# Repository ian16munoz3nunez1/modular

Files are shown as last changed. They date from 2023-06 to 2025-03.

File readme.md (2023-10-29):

# Proyecto Modular (Equipo Amistad) 😉

## Archivos binarios

- [MicroPython](https://micropython.org/download/esp32)
- [esp32cam](https://github.com/lemariva/micropython-camera-driver)

## Librerias Python

- ***sockets*** `pip install sockets`
- ***opencv*** `pip install opencv-contrib-python`
- ***numpy*** `pip install numpy` 
- ***matplotlib*** `pip install matplotlib`
- ***thonny*** `pip install thonny-esp`
- ***pyserial*** `pip install pyserial`
- ***esptool*** `pip install esptool`
- ***ampy*** `pip install adafruit-ampy`

## Comandos y programas

### Windows

Listar los dispositivos conectados a los puertos:
`py -m serial.tools.list_ports`

Borrar la memoria del esp32:
`esptool --chip esp32 --port COM* erase_flash`

Cargar el archivo binario a la placa esp32:
`esptool --chip esp32 --port COM* --baud 460800 write_flash -z 0x1000 <esp32version>.bin`

Cargar un archivo *Python* a la esp32:
`ampy --port COM* put main.py`

Obtener el contenido de un archivo:
`ampy --port COM* get main.py`

Listar los archivos dentro de la placa:
`ampy --port COM* ls`

Crear conexión serial con la esp32 en PuTTY:

- Puerto: ***COM\****
- Velocidad: ***115200 bauds***

#### Configurar Thonny para esp32cam

Ir a ***Thonny***:

`Tools > Open Thonny data folder...`

Agregar al archivo ***configuration.ini*** en la sección ***ESP32***

```
[ESP32]
rts = False
dtr = False
```

### Linux

Listar los dispositivos conectados a los puertos:
`python3 -m serial.tools.list_ports`

Borrar la memoria del esp32:
`esptool.py --chip esp32 --port /dev/ttyUSB* erase_flash`

Cargar el archivo binario a la placa esp32:
`esptool.py --chip esp32 --port /dev/ttyUSB* --baud 460800 write_flash -z 0x1000 <esp32version>.bin`

Cargar un archivo *Python* a la esp32:
`ampy --port /dev/ttyUSB* put main.py`

Obtener el contenido de un archivo:
`ampy --port /dev/ttyUSB* get main.py`

Listar los archivos dentro de la placa:
`ampy --port /dev/ttyUSB* ls`

Crear conexión serial con la esp32:
`picocom /dev/ttyUSB* -b 115200`

Crear conexión serial con la esp32cam:
`picocom /dev/ttyUSB* -b 115200 --lower-dtr --lower-rts`

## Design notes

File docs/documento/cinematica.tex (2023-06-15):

\sffamily\large\justify

\pagenumbering{arabic}

\section{Cinemática directa}

\subsection{Modelado del \emph{youBot Arm}}

\begin{figure}[h!]
    \centering
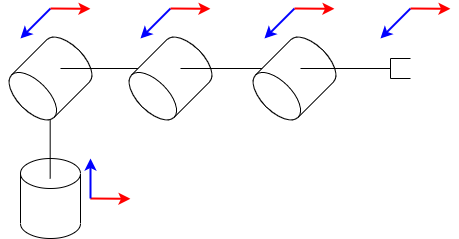
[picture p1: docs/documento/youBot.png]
    
    \caption{\sffamily youBot Arm}
    \label{fig:youBotArmModel}
\end{figure}

\subsection{Fórmulas y propiedades}

\begin{equation*}
    ^{n-1}T_n =
    \begin{bmatrix}
        C_{\theta_n} & -S_{\theta_n}C_{\alpha_n} & S_{\theta_n}S_{\alpha_n} & a_nC_{\theta_n} \\
        S_{\theta_n} & C_{\theta_n}C_{\alpha_n} & -C_{\theta_n}S_{\alpha_n} & a_nS_{\theta_n} \\
        0 & S_{\alpha_n} & C_{\alpha_n} & d_n \\
        0 & 0 & 0 & 1
    \end{bmatrix}
\end{equation*}

\begin{equation*}
    \begin{split}
        \sin(\alpha \pm \beta) & = \sin(\alpha)\cos(\beta) \pm \cos(\alpha)\sin(\beta) \\
        \cos(\alpha \pm \beta) & = \cos(\alpha)\cos(\beta) \mp \sin(\alpha)\sin(\beta)
    \end{split}
\end{equation*}

\newpage
\subsection{Tabla de parámetros \emph{Denavit-Hartenberg}}

\begin{table}[h!]
    \centering\sffamily\large

    \begin{tabular}{|c|c|c|c|c|}
        \hline
        & $\alpha$ & $a$ & $d$ & $\theta$ \\
        \hline
        1 & $\frac{\pi}{2}$ & $0$ & $d_1$ & $0$ \\
        \hline
        2 & $0$ & $a_2$ & $0$ & $0$ \\
        \hline
        3 & $0$ & $a_3$ & $0$ & $0$ \\
        \hline
        4 & $0$ & $a_4$ & $0$ & $0$ \\
        \hline
    \end{tabular}

    \caption{\sffamily Tabla de parámetros \emph{Denavit-Hartenberg}}
    \label{tab:tablaDH}
\end{table}

\subsection{Matrices de transformación}

\begin{equation*}
    \tcboxmath[colback=white, colframe=black]{
    ^0T_1 =
    \begin{bmatrix}
        C_1 & 0 & S_1 & 0 \\
        S_1 & 0 & -C_1 & 0 \\
        0 & 0 & 1 & 0 \\
        0 & 0 & 0 & 1
    \end{bmatrix}
    }
    \quad\quad
    ^1T_2 =
    \begin{bmatrix}
        C_2 & -S_2 & 0 & a_2C_2 \\
        S_2 & C_2 & 0 & a_2S_2 \\
        0 & 0 & 1 & 0 \\
        0 & 0 & 0 & 1
    \end{bmatrix}
\end{equation*}

\begin{equation*}
    ^2T_3 =
    \begin{bmatrix}
        C_3 & -S_3 & 0 & a_3C_3 \\
        S_3 & C_3 & 0 & a_3S_3 \\
        0 & 0 & 1 & 0 \\
        0 & 0 & 0 & 1
    \end{bmatrix}
    \quad\quad
    ^3T_4 =
    \begin{bmatrix}
        C_4 & -S_4 & 0 & a_4C_4 \\
        S_4 & C_4 & 0 & a_4S_4 \\
        0 & 0 & 1 & 0 \\
        0 & 0 & 0 & 1
    \end{bmatrix}
\end{equation*}

\begin{equation*}
    ^0T_4 = {^0T_1} \, {^1T_2} \, {^2T_3} \, {^3T_4}
\end{equation*}

\newpage
\subsection{Cinemática directa del \emph{youBot Arm}}

\begin{equation*}
    \tcboxmath[colback=white, colframe=black]{
    ^0T_2 =
    \begin{bmatrix}
        C_1C_2 & -C_1S_2 & S_1 & a_2C_1C_2 \\
        S_1C_2 & -S_1S_2 & -C_1 & a_2S_1C_2 \\
        S_2 & C_2 & 0 & a_2S_2 + d_1 \\
        0 & 0 & 0 & 1
    \end{bmatrix}
    }
\end{equation*}

{\small
\begin{equation*}
    ^0T_3 =
    \begin{bmatrix}
        C_1C_2C_3 - C_1S_2S_3 & -C_1C_2S_3 - C_1S_2C_3 & S_1 & a_3C_1C_2C_3 - a_3C_1S_2S_3 + a_2C_1C_2 \\
        S_1C_2C_3 - S_1S_2S_3 & -S_1C_2S_3 - S_1S_2C_3 & -C_1 & a_3S_1C_2C_3 - a_3S_1S_2S_3 + a_2S_1C_2 \\
        S_2C_3 + C_2S_3 & -S_2S_3 + C_2C_3 & 0 & a_3S_2C_3 + a_3C_2S_3 + a_2S_2 + d_1 \\
        0 & 0 & 0 & 1
    \end{bmatrix}
\end{equation*}
}

\begin{equation*}
    \tcboxmath[colback=white, colframe=black]{
    ^0T_3 =
    \begin{bmatrix}
        C_1C_{23} & -C_1S_{23} & S_1 & a_3C_1C_{23} + a_2C_1C_2 \\
        S_1C_{23} & -S_1S_{23} & -C_1 & a_3S_1C_{23} + a_2S_1C_2 \\
        S_{23} & C_{23} & 0 & a_3S_{23} + a_2S_2 + d_1 \\
        0 & 0 & 0 & 1
    \end{bmatrix}
    }
\end{equation*}

{\scriptsize
\begin{equation*}
    ^0T_4 =
    \begin{bmatrix}
        C_1C_{23}C_4 - C_1S_{23}S_4 & -C_1C_{23}S_4 - C_1S_{23}C_4 & S_1 & a_4C_1C_{23}C_4 - a_4C_1S_{23}S_4 + a_3C_1C_{23} + a_2C_1C_2 \\
        S_1C_{23}C_4 - S_1S_{23}S_4 & -S_1C_{23}S_4 - S_1S_{23}C_4 & -C_1 & a_4S_1C_{23}C_4 - a_4S_1S_{23}S_4 + a_3S_1C_{23} + a_2S_1C_2 \\
        S_{23}C_4 + C_{23}S_4 & -S_{23}S_4 + C_{23}C_4 & 0 & a_4S_{23}C_4 + a_4C_{23}S_4 + a_3S_{23} + a_2S_2 + d_1 \\
        0 & 0 & 0 & 1
    \end{bmatrix}
\end{equation*}
}

\begin{equation*}
    ^0T_4 =
    \begin{bmatrix}
        C_1C_{234} & -C_1S_{234} & S_1 & a_4C_1C_{234} + a_3C_1C_{23} + a_2C_1C_2 \\
        S_1C_{234} & -S_1S_{234} & -C_1 & a_4S_1C_{234} + a_3S_1C_{23} + a_2C_1C_2 \\
        S_{234} & C_{234} & 0 & a_4S_{234} + a_3S_{23} + a_2S_2 + d_1 \\
        0 & 0 & 0 & 1
    \end{bmatrix}
\end{equation*}

\begin{equation*}
    \tcboxmath[colback=white, colframe=black]{
    ^0T_4 =
    \begin{bmatrix}
        C_1C_{234} & -C_1S_{234} & S_1 & C_1 ( a_4C_{234} + a_3C_{23} + a_2C_2 ) \\
        S_1C_{234} & -S_1S_{234} & -C_1 & S_1 ( a_4C_{234} + a_3C_{23} + a_2C_2 ) \\
        S_{234} & C_{234} & 0 & a_4S_{234} + a_3S_{23} + a_2S_2 + d_1 \\
        0 & 0 & 0 & 1
    \end{bmatrix}
    }
\end{equation*}

\newpage
\subsection{Cinemática directa de la plataforma omnidireccional}

\begin{equation*}
    \begin{bmatrix}
        \dot{x} \\
        \dot{y} \\
        \dot{\theta}
    \end{bmatrix} =
    \begin{bmatrix}
        \cos(\theta) & -\sin(\theta) & 0 \\
        \sin(\theta) & \cos(\theta) & 0 \\
        0 & 0 & 1
    \end{bmatrix}
    \begin{bmatrix}
        1 & -1 & -(L+l) \\
        1 & 1 & (L+l) \\
        1 & 1 & -(L+l) \\
        1 & -1 & (L+l)
    \end{bmatrix}^\dagger
    \begin{bmatrix}
        v_1 \\
        v_2 \\
        v_3 \\
        v_4
    \end{bmatrix}
\end{equation*}

\subsection{Cinemática inversa de la plataforma omnidireccional}

\begin{equation*}
    \begin{bmatrix}
        v_1 \\
        v_2 \\
        v_3 \\
        v_4
    \end{bmatrix} =
    \begin{bmatrix}
        1 & -1 & -(L+l) \\
        1 & 1 & (L+l) \\
        1 & 1 & -(L+l) \\
        1 & -1 & (L+l)
    \end{bmatrix}
    \begin{bmatrix}
        \cos(\theta) & -\sin(\theta) & 0 \\
        \sin(\theta) & \cos(\theta) & 0 \\
        0 & 0 & 1
    \end{bmatrix}^\top
    \begin{bmatrix}
        \dot{x} \\
        \dot{y} \\
        \dot{\theta}
    \end{bmatrix}
\end{equation*}

\begin{equation*}
    \begin{bmatrix}
        v_1 \\
        v_2 \\
        v_3 \\
        v_4
    \end{bmatrix} =
    \begin{bmatrix}
        \sqrt{2}\sin(\alpha) & -\sqrt{2}\cos(\alpha) & -(L+l) \\
        \sqrt{2}\cos(\alpha) & \sqrt{2}\sin(\alpha) & (L+l) \\
        \sqrt{2}\cos(\alpha) & \sqrt{2}\sin(\alpha) & -(L+l) \\
        \sqrt{2}\sin(\alpha) & -\sqrt{2}\cos(\alpha) & (L+l)
    \end{bmatrix}
    \begin{bmatrix}
        \dot{x} \\
        \dot{y} \\
        \dot{\theta}
    \end{bmatrix}
\end{equation*}

\begin{equation*}
    \alpha = \theta + \frac{\pi}{4}
\end{equation*}

\newpage
\subsection{Cinemática directa desde el origen hasta el efector final}

\renewcommand{\labelitemi}{$\bullet$}
\begin{itemize}
    \item \textbf{w:} Eje coordenado del origen.
    \item \textbf{p:} Eje coordenado adherido a la plataforma.
    \item \textbf{b:} Eje coordenado de la base del manipulador.
    \item \textbf{e:} Eje coordenado del actuador final.
\end{itemize}

\begin{equation*}
    ^wT_e = {^wT_p} \, {^pT_b} \, {^bT_e}
\end{equation*}

\begin{equation*}
    \tcboxmath[colback=white, colframe=black]{
    ^wT_p =
    \begin{bmatrix}
        \cos(\theta_p) & -\sin(\theta_p) & 0 & x_p \\
        \sin(\theta_p) & \cos(\theta_p) & 0 & y_p \\
        0 & 0 & 1 & 0 \\
        0 & 0 & 0 & 1
    \end{bmatrix}
    }
\end{equation*}

\hspace{0.5cm} Con $x_p$ y $y_p$ como la posición del robot y $\theta_p$ como la
orientación.

\begin{equation*}
    \tcboxmath[colback=white, colframe=black]{
    ^pT_b =
    \begin{bmatrix}
        1 & 0 & 0 & 0.170 \\
        0 & 1 & 0 & 0 \\
        0 & 0 & 1 & 0.060 \\
        0 & 0 & 0 & 1
    \end{bmatrix}
    }
\end{equation*}

\begin{equation*}
    \tcboxmath[colback=white, colframe=black]{
    ^bT_e = {^0T_4}
    }
\end{equation*}

\begin{equation*}
    \tcboxmath[colback=white, colframe=black]{
    ^wT_b =
    \begin{bmatrix}
        \cos(\theta_p) & -\sin(\theta_p) & 0 & 0.170\cos(\theta_p) + x_p \\
        \sin(\theta_p) & \cos(\theta_p) & 0 & 0.170\sin(\theta_p) + y_p \\
        0 & 0 & 1 & 0.060 \\
        0 & 0 & 0 & 1
    \end{bmatrix}
    }
\end{equation*}

\newpage
{\normalsize
\begin{equation*}
    \tcboxmath[colback=white, colframe=black]{
    \begin{split}
        x & = C_\theta C_1( a_4C_{234}+a_3C_{23}+a_2C_2 ) - S_\theta S_1( a_4C_{234}+a_3C_{23}+a_2C_2 ) + 0.170C_\theta + x_p \\
        y & = S_\theta C_1( a_4C_{234}+a_3C_{23}+a_2C_2 ) + C_\theta S_1( a_4C_{234}+a_3C_{23}+a_2C_2 ) + 0.170S_\theta + y_p \\
        z & = a_4S_{234} + a_3S_{23} + a_2S_2 + d_1 + 0.060 \\
    \end{split}
    }
\end{equation*}
}

{\normalsize
\begin{equation*}
    \tcboxmath[colback=white, colframe=black]{
    ^wT_e =
    \begin{bmatrix}
        C_\theta C_1C_{234} - S_\theta S_1C_{234} & -C_\theta C_1S_{234} + S_\theta S_1S_{234} & C_\theta S_1 + S_\theta C_1 & x \\
        S_\theta C_1 C_{234} + C_\theta S_1C_{234} & -S_\theta C_1S_{234} - C_\theta S_1S_{234} & S_\theta S_1 - C_\theta C_1 & y \\
        S_{234} & C_{234} & 0 & z \\
        0 & 0 & 0 & 1
    \end{bmatrix}
    }
\end{equation*}
}

{\normalsize
\begin{equation*}
    \tcboxmath[colback=white, colframe=black]{
    ^wT_e =
    \begin{bmatrix}
        C_{\theta 1}C_{234} & -C_{\theta 1}S_{234} & S_{\theta 1} & C_{\theta 1} ( a_4C_{234} + a_3C_{23} + a_2C_2 ) + 0.170C_\theta + x_p \\
        S_{\theta 1}C_{234} & -S_{\theta 1}S_{234} & -C_{\theta 1} & S_{\theta 1} ( a_4C_{234} + a_3C_{23} + a_2C_2 ) + 0.170S_\theta + y_p \\
        S_{234} & C_{234} & 0 & a_4S_{234} + a_3S_{23} + a_2S_2 + d_1 + 0.060 \\
        0 & 0 & 0 & 1
    \end{bmatrix}
    }
\end{equation*}
}

\subsection{Cinemática diferencial}

\begin{equation*}
    J_v(q) =
    \begin{bmatrix}
        \dfrac{\partial p_1(q)}{\partial q_1} & \dfrac{\partial p_1(q)}{\partial q_2} & \dotsc & \dfrac{\partial p_1(q)}{\partial q_n} \\
        \dfrac{\partial p_2(q)}{\partial q_1} & \dfrac{\partial p_2(q)}{\partial q_2} & \dotsc & \dfrac{\partial p_2(q)}{\partial q_n} \\
        \vdots & \vdots & \ddots & \vdots \\
        \dfrac{\partial p_m(1)}{\partial q_1} & \dfrac{\partial p_m(q)}{\partial q_2} & \dotsc & \dfrac{\partial p_m(q)}{\partial q_n}
    \end{bmatrix}
\end{equation*}

\begin{equation*}
    \begin{split}
        t_x & = C_{\theta 1} ( a_4C_{234} + a_3C_{23} + a_2C_2 ) + 0.170C_\theta + x_p \\
        t_y & = S_{\theta 1} ( a_4C_{234} + a_3C_{23} + a_2C_2 ) + 0.170S_\theta + y_p \\
        t_z & = a_4S_{234} + a_3S_{23} + a_2S_2 + d_1 + 0.060
    \end{split}
\end{equation*}

\newpage
\begin{equation*}
    \begin{split}
        \frac{\partial t_x}{\partial x_p} & = 1 \\
        \frac{\partial t_x}{\partial y_p} & = 0 \\
        \frac{\partial t_x}{\partial \theta_p} & = -S_{\theta 1} ( a_4C_{234}+a_3C_{23}+a_2C_2 ) - 0.170S_\theta \\
        \frac{\partial t_x}{\partial \theta_1} & = -S_{\theta 1} ( a_4C_{234}+a_3C_{23}+a_2C_2 ) \\
        \frac{\partial t_x}{\partial \theta_2} & = -C_{\theta 1} ( a_4S_{234}+a_3S_{23}+a_2S_2 ) \\
        \frac{\partial t_x}{\partial \theta_3} & = -C_{\theta 1} ( a_4S_{234}+a_3S_{23} ) \\
        \frac{\partial t_x}{\partial \theta_4} & = -a_4C_{\theta 1}S_{234}
    \end{split}
\end{equation*}

\begin{equation*}
    \begin{split}
        \frac{\partial t_y}{\partial x_p} & = 0 \\
        \frac{\partial t_y}{\partial y_p} & = 1 \\
        \frac{\partial t_y}{\partial \theta_p} & = C_{\theta 1} ( a_4C_{234} + a_3C_{23} + a_2C_2 ) + 0.170C_\theta \\
        \frac{\partial t_y}{\partial \theta_1} & = C_{\theta 1} ( a_4C_{234} + a_3C_{23} + a_2C_2 )  \\
        \frac{\partial t_y}{\partial \theta_2} & = -S_{\theta 1} ( a_4S_{234} + a_3S_{23} + a_2S_2 ) \\
        \frac{\partial t_y}{\partial \theta_3} & = -S_{\theta 1} ( a_4S_{234} + a_3S_{23} ) \\
        \frac{\partial t_y}{\partial \theta_4} & = -a_4S_{\theta 1}S_{234}
    \end{split}
\end{equation*}

\newpage
\begin{equation*}
    \begin{split}
        \frac{\partial t_z}{\partial x_p} & = 0 \\
        \frac{\partial t_z}{\partial x_p} & = 0 \\
        \frac{\partial t_z}{\partial x_p} & = 0 \\
        \frac{\partial t_z}{\partial \theta_1} & = 0 \\
        \frac{\partial t_z}{\partial \theta_2} & = a_4C_{234} + a_3C_{23} + a_2C_2 \\
        \frac{\partial t_z}{\partial \theta_3} & = a_4C_{234} + a_3C_{23} \\
        \frac{\partial t_z}{\partial \theta_4} & = a_4C_{234}
    \end{split}
\end{equation*}

\begin{equation*}
    J_v =
    \begin{bmatrix}
        \dfrac{\partial t_x}{\partial x_p} & \dfrac{\partial t_x}{\partial y_p} & \dfrac{\partial t_x}{\partial \theta_p} & \dfrac{\partial t_x}{\partial \theta_1} & \dfrac{\partial t_x}{\partial \theta_2} & \dfrac{\partial t_x}{\partial \theta_3} & \dfrac{\partial t_x}{\partial \theta_4} \\
        \dfrac{\partial t_y}{\partial x_p} & \dfrac{\partial t_y}{\partial y_p} & \dfrac{\partial t_y}{\partial \theta_p} & \dfrac{\partial t_y}{\partial \theta_1} & \dfrac{\partial t_y}{\partial \theta_2} & \dfrac{\partial t_y}{\partial \theta_3} & \dfrac{\partial t_y}{\partial \theta_4} \\
        \dfrac{\partial t_z}{\partial x_p} & \dfrac{\partial t_z}{\partial y_p} & \dfrac{\partial t_z}{\partial \theta_p} & \dfrac{\partial t_z}{\partial \theta_1} & \dfrac{\partial t_z}{\partial \theta_2} & \dfrac{\partial t_z}{\partial \theta_3} & \dfrac{\partial t_z}{\partial \theta_4} \\
    \end{bmatrix}
\end{equation*}

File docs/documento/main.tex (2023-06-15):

\documentclass[12pt, oneside]{article}
\usepackage[T1]{fontenc}
\usepackage[spanish, es-tabla, es-lcroman]{babel}
\usepackage[utf8]{inputenc}
\usepackage[document]{ragged2e}
\usepackage{tcolorbox}
\tcbuselibrary{theorems}
\usepackage{cancel}
\usepackage{amssymb}
\usepackage{amsmath}
\usepackage{mathrsfs}
\usepackage{wrapfig}
\usepackage{fancyhdr}
\usepackage{colortbl}
\usepackage{diagbox}
\usepackage{longtable}
\usepackage{graphicx}
\usepackage{subcaption}
\usepackage{xcolor}
\usepackage{tikz}
\usetikzlibrary{positioning}
\usepackage{multicol}
\usepackage{multirow}
\usepackage{lastpage}
\usepackage{pdfpages}
\usepackage{listings}
\usepackage{blindtext}
\usepackage{fontawesome}
\spanishdecimal{.}
\usepackage[explicit]{titlesec}
\usepackage[colorlinks=true, linkcolor=black, citecolor=black, urlcolor=blue]{hyperref}
\usepackage[a4paper, total={16cm, 24cm}]{geometry}
\pagestyle{fancy}
\lhead{Equipo amistad}
\rhead{Modular 2023-B}
\lhead{INCE - INRO}
\rhead{CUCEI}
\renewcommand{\headrulewidth}{1pt}
\renewcommand{\footrulewidth}{1pt}
\def\columnseprulecolor{\color{magenta}}

\setlength{\headheight}{14.49998pt}
\setlength{\columnseprule}{1pt}

\begin{document}

\include{portada}

\include{cinematica}

\include{control}

\end{document}

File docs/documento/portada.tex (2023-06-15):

\begin{titlepage}
    \pagenumbering{roman}
    \centering
    {\bfseries\LARGE Universidad de Guadalajara \par}
    \vfill
    {
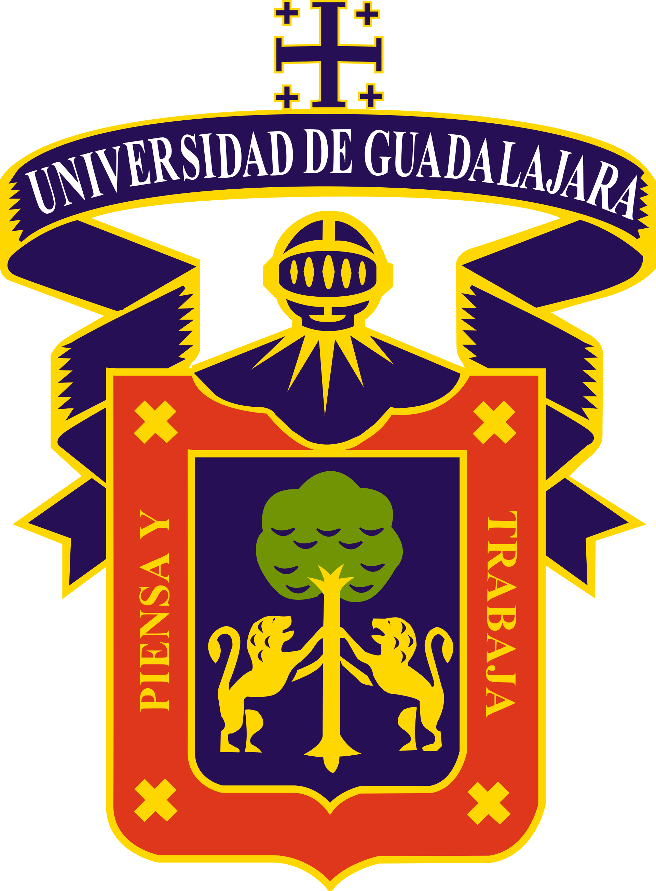
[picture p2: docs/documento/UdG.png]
        
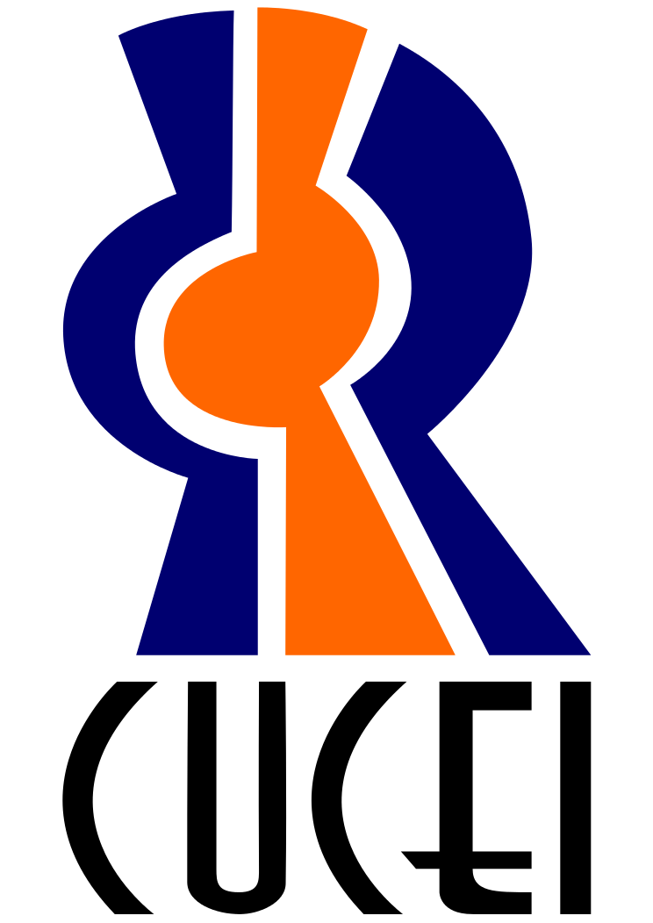
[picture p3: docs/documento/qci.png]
        
        \par
    }
    \vfill
    {\bfseries\LARGE CUCEI \par}
    \vfill
    {\bfseries\LARGE Proyecto Modular \par}
    \vfill
    {\bfseries\LARGE Equipo Amistad \par}
    \vfill
    {\bfseries\LARGE Briseño García Jorge Beto \par}
    \vfill
    {\bfseries\LARGE Briseño García Edna Elizabeth \par}
    \vfill
    {\bfseries\LARGE Muñoz Nuñez Ian Emmanuel \par}
\end{titlepage}

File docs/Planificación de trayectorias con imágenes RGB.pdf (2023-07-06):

# Planificación de trayectorias con imágenes RGB

Dr. José de Jesús Hernández Barragán josed.hernandezb@academicos.udg.mx

1

# Introducción

Objetivo: Generar una trayectoria con datos obtenidos desde una cámara RGB, para poder aplicar un seguimiento de trayectoria en el plano.

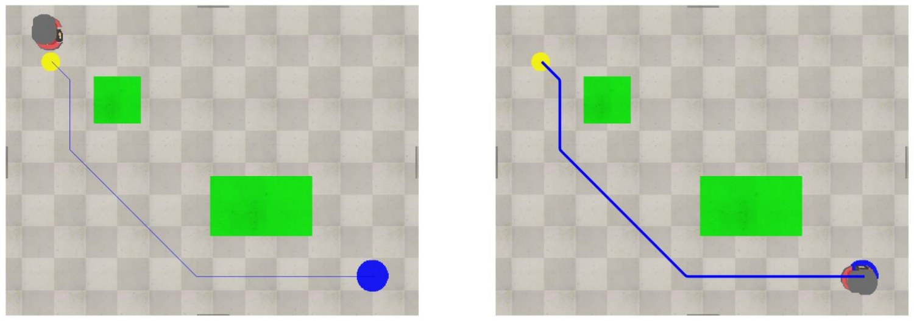
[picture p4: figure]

2

# Introducción (continuación)

Para crear una mapa de entorno se propone utilizar rejillas de ocupación con base en segmentación por color.

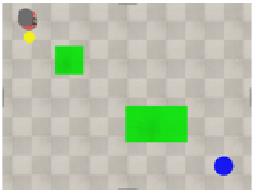
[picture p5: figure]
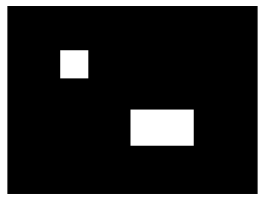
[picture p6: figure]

Dada una imagen RGB, se pueden segmentar los obstáculos para
crear un mapa de entorno. En un rejilla de ocupación, valores
en 0 representan caminos libres, mientras que valores en 1
representan obstáculos. | 3
Imagen RGB | Mapa en rejillas de ocupación

# Introducción (continuación)

Dado un mapa en rejillas de ocupación, se recomienda aplicar primero una dilatación al mapa y después aplicar la planificación de la trayectoria.

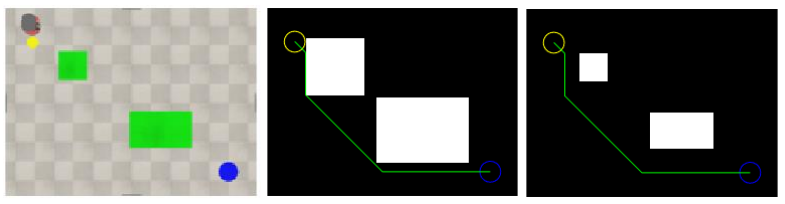
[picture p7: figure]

La dilatación es necesaria para que el robot móvil no colisione
con los obstáculos del ambiente. El inicio y final de la trayectoria
se pueden encontrar con segmentación por color. | 4
Imagen RGB | Mapa dilatado | Mapa original

# Introducción (continuación)

La trayectoria generada por el algoritmo de planificación contiene valores en pixeles.

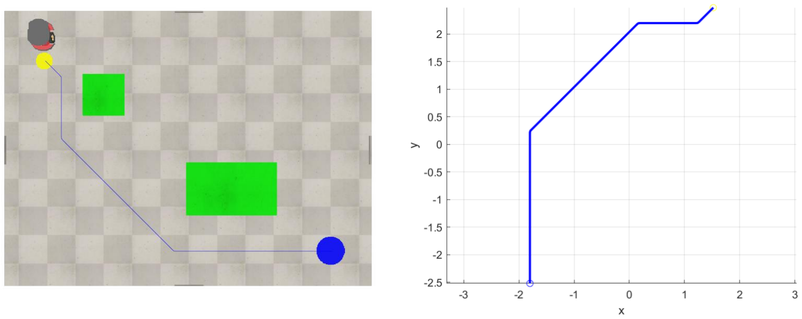
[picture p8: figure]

Los valores en pixeles se convierten a valores en el plano para que el robot móvil los pueda seguir con una técnica de control.

5

Trayectoria en la imagen | Trayectoria en el plano

## Segmentación por color

La segmentación por color consiste en clasificar los pixeles exclusivamente por su color.

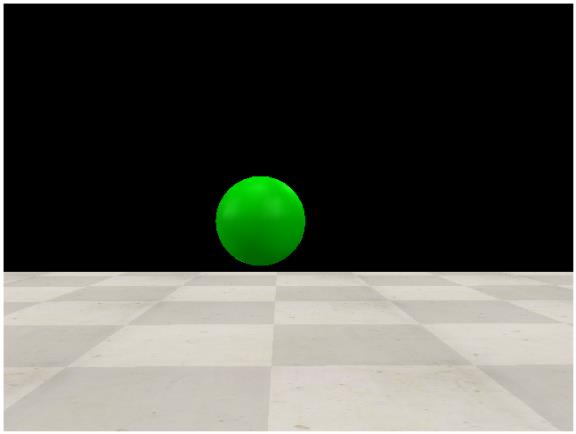
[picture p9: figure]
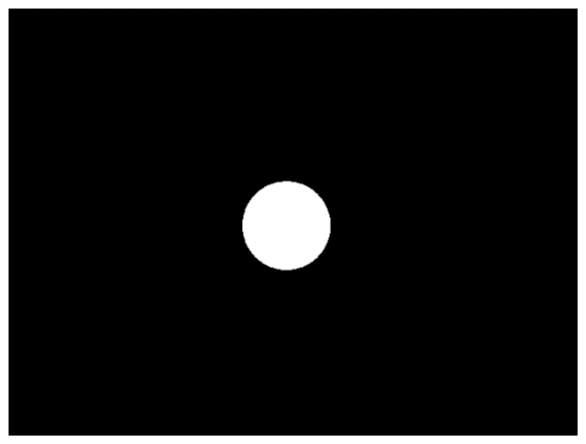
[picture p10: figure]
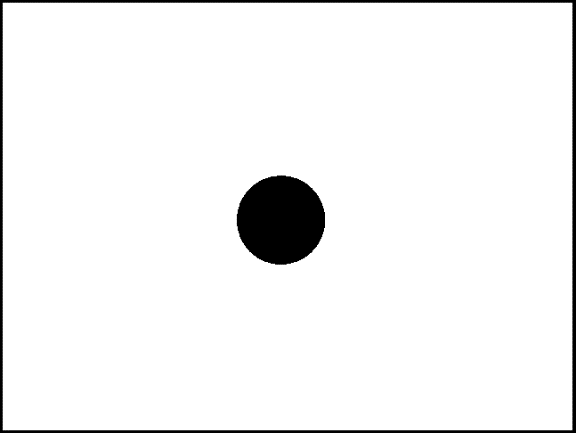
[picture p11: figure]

En esta presentación me muestra un método de umbralización binaria por intensidad del pixel.

6

Imagen RGB | Ejemplo 1 de segmentación

Ejemplo 2 de
segmentación

## Segmentación por color (continuación)

El método de umbralización binaria considerado se basa en el uso de la ecuación reducida de la esfera.

7

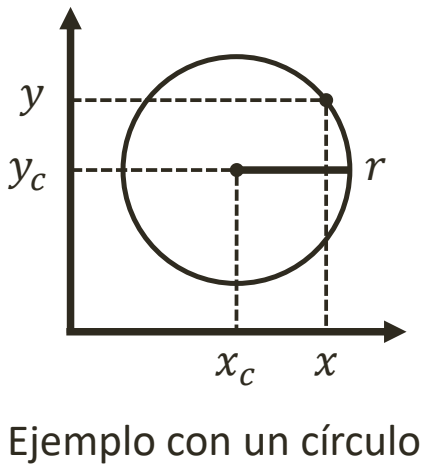
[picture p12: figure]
Ejemplo con un círculo
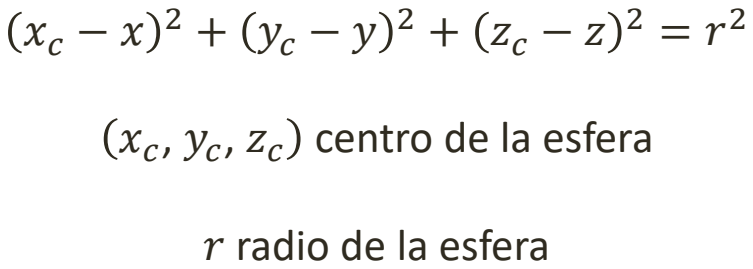
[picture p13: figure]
, zc centro de la esfera; r radio de la esfera

## Segmentación por color (continuación)

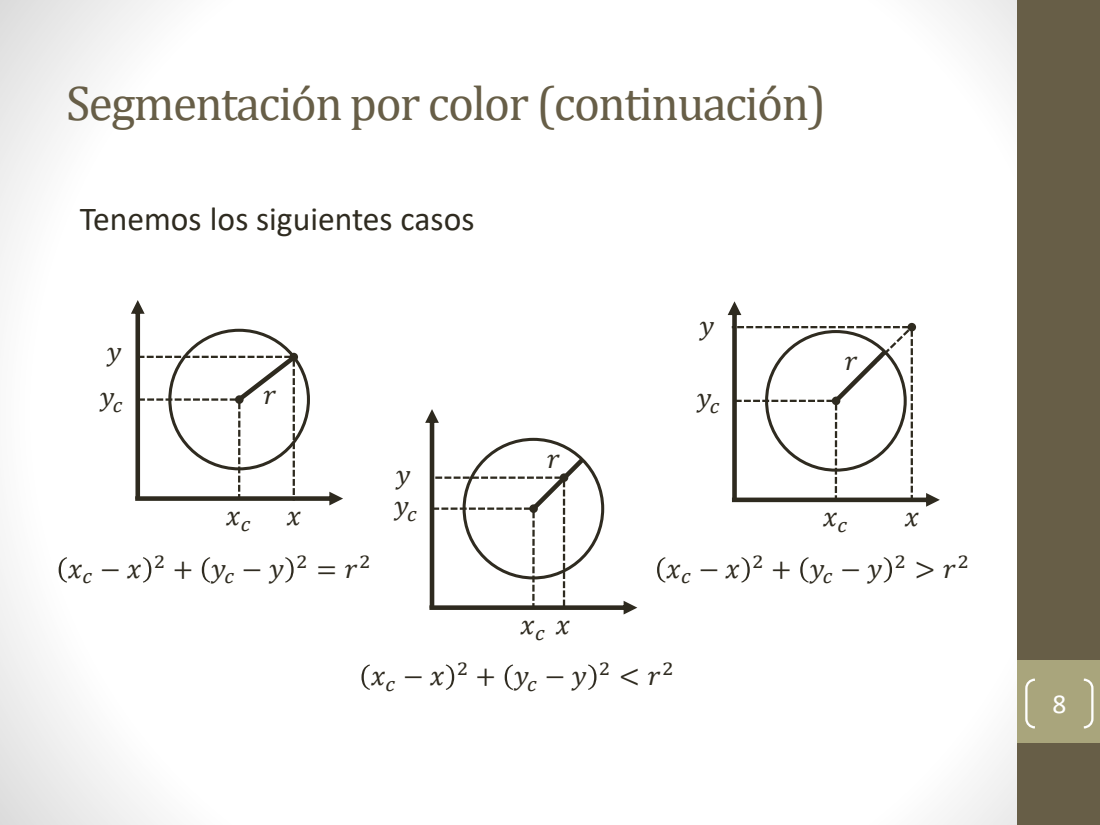
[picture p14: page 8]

Tenemos los siguientes casos

## Segmentación por color (continuación)

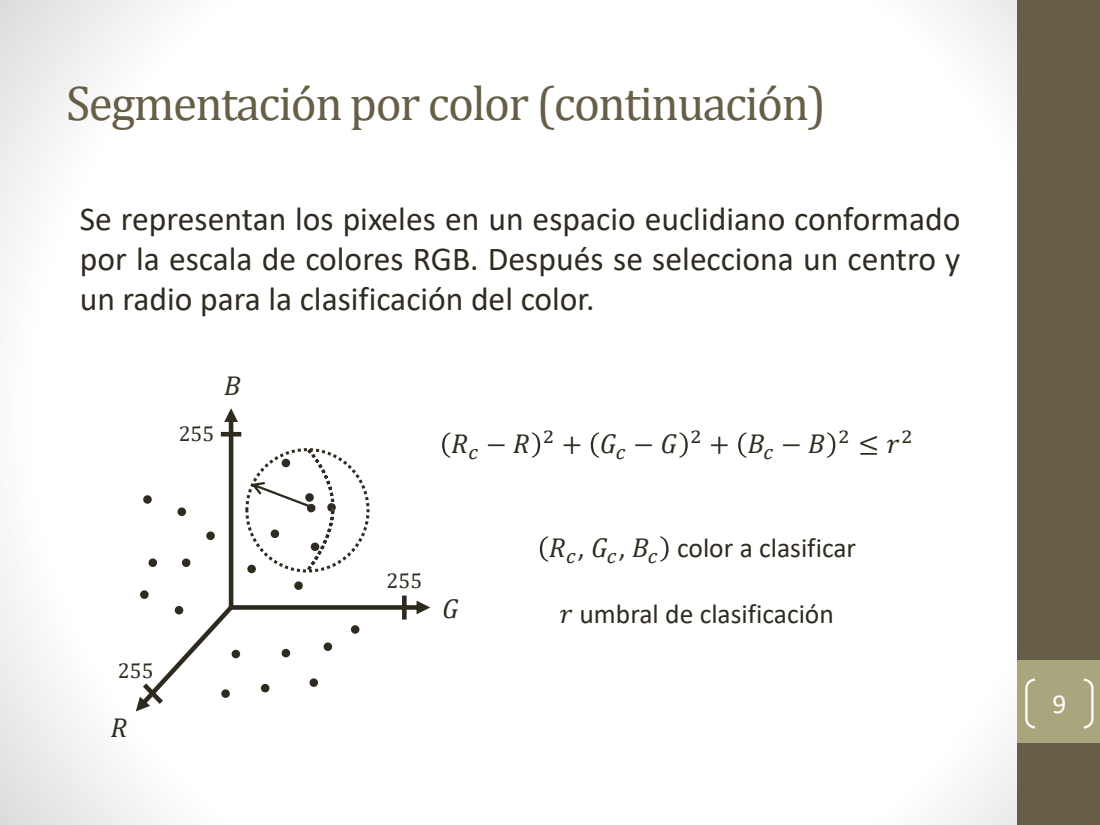
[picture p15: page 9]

Se representan los pixeles en un espacio euclidiano conformado
por la escala de colores RGB. Después se selecciona un centro y
un radio para la clasificación del color.

, Bc color a clasificar

r umbral de clasificación

## Segmentación por color (continuación)

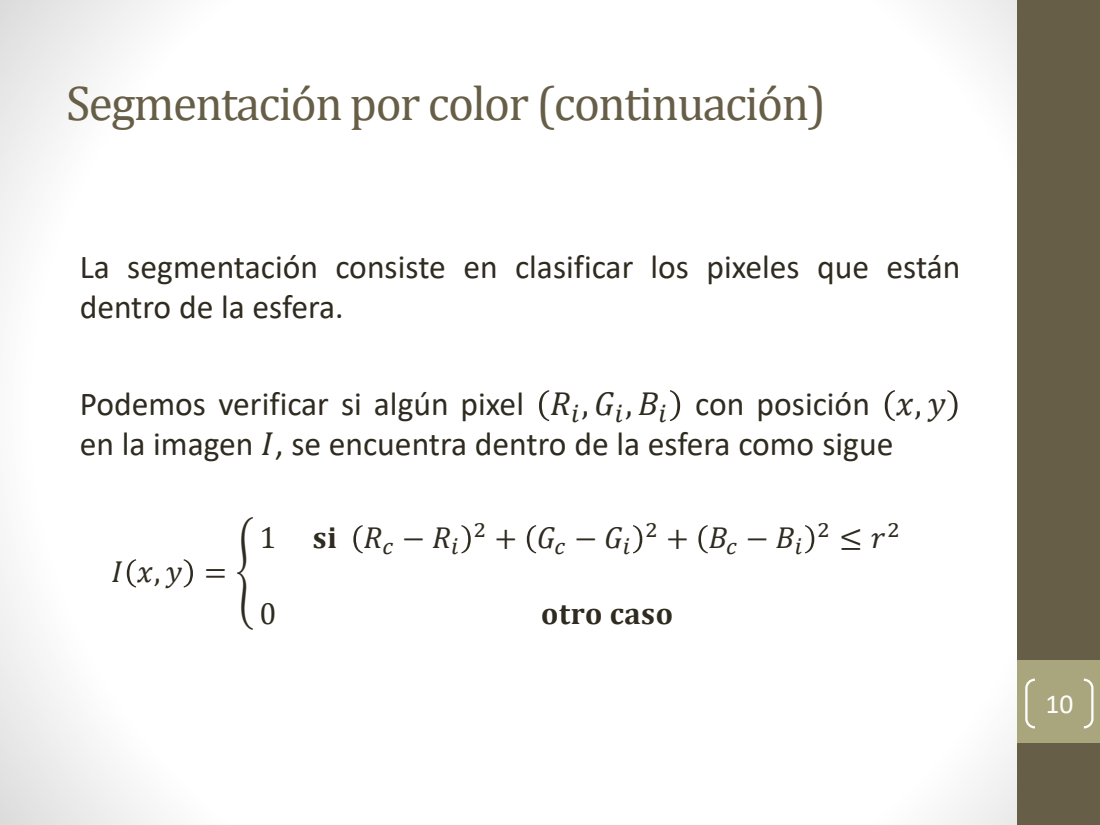
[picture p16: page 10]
otro caso

La segmentación consiste en clasificar los pixeles que están
dentro de la esfera.

Podemos verificar si algún pixel Ri
en la imagen I, se encuentra dentro de la esfera como sigue

,Bi con posición x, y

## Mapa de entorno

Se aplica la segmentación para representar los obstáculos en la rejilla de ocupación, pero también se recomienda identificar el inicio y final de la trayectoria con otro color.

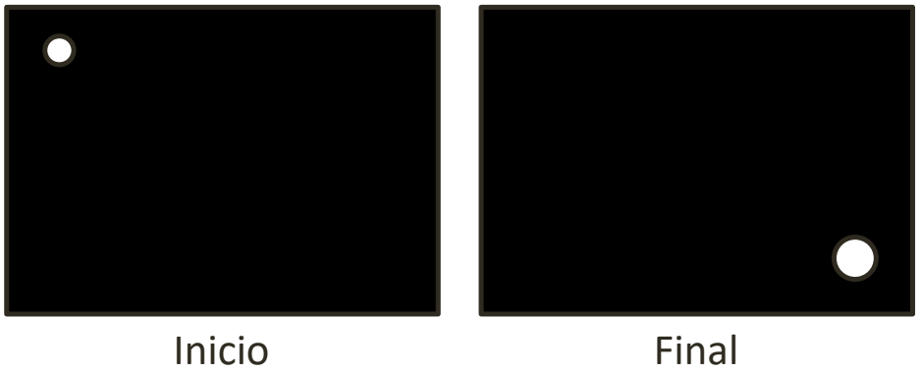
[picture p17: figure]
Inicio; Final

11

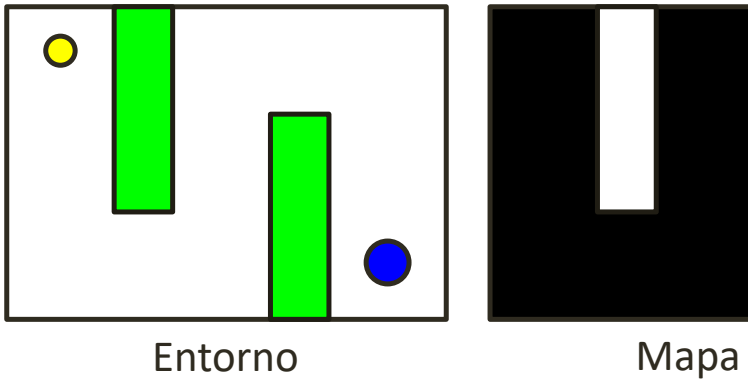
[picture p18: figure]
Entorno; Mapa

## Mapa de entorno (continuación)

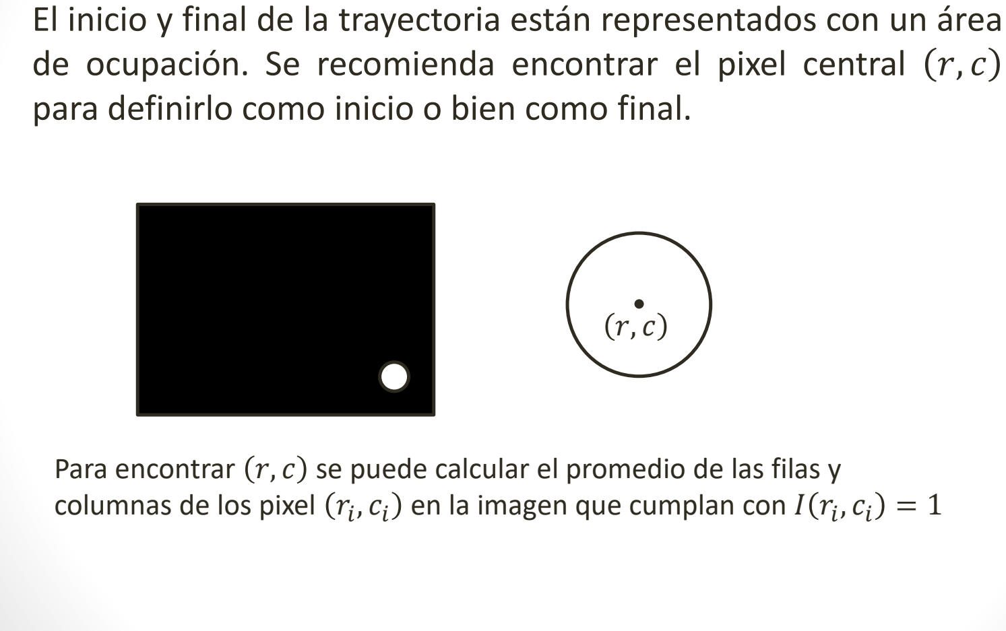
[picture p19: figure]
columnas de los pixel ri; , ci en la imagen que cumplan con I ri

El inicio y final de la trayectoria están representados con un área de ocupación. Se recomienda encontrar el pixel central r, c para definirlo como inicio o bien como final.

12

Para encontrar r, c se puede calcular el promedio de las filas y

## Mapa de entorno (continuación)

Se recomienda trabajar con imágenes pequeñas y no de alta resolución. Por esta razón, se propone primero escalar la imagen del entorno y después construir las rejillas de ocupación.

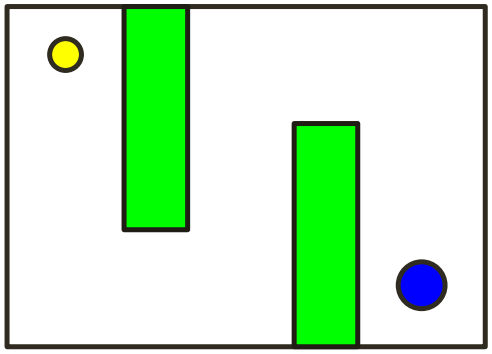
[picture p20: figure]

Encontrar la trayectoria en un mapa con rejillas de ocupación mas chico, requiere de menor coste computacional.

13

## Pixeles en un plano

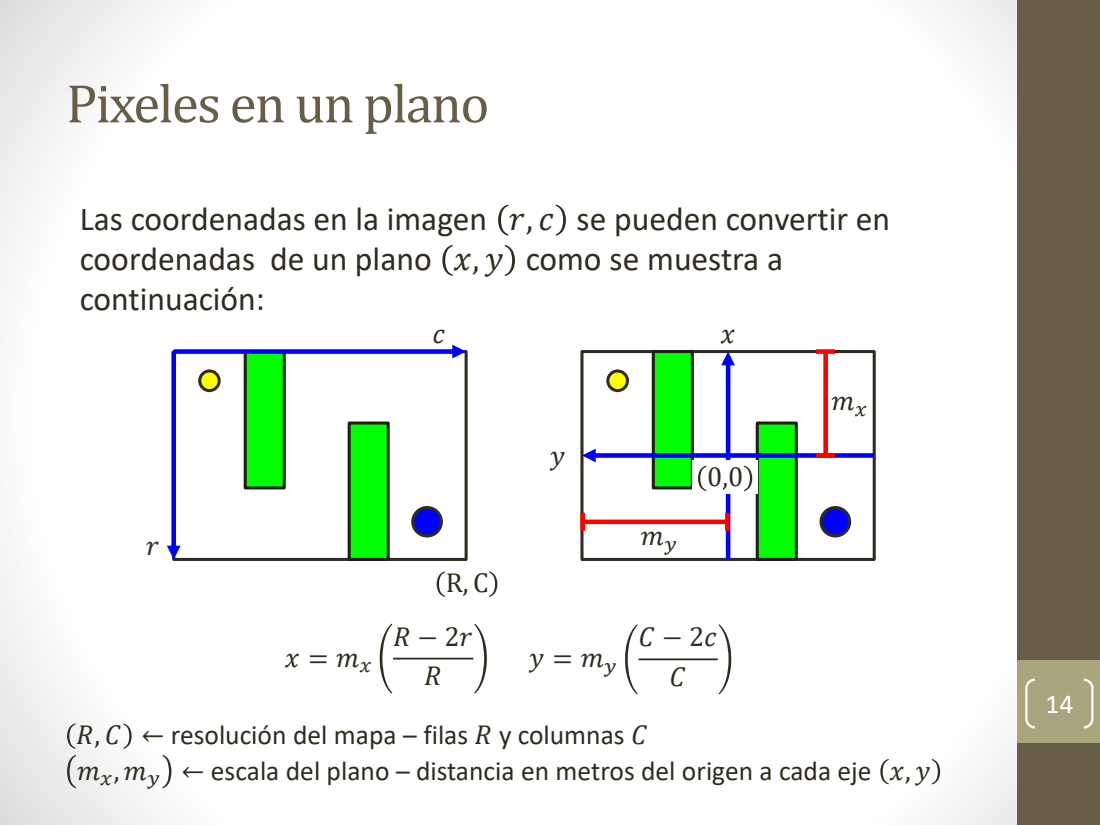
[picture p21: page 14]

Las coordenadas en la imagen r, c se pueden convertir en
coordenadas de un plano x, y como se muestra a
continuación:

R, C ← resolución del mapa – filas R y columnas C
mx, my ← escala del plano – distancia en metros del origen a cada eje x, y

## Pixeles en un plano (continuación)

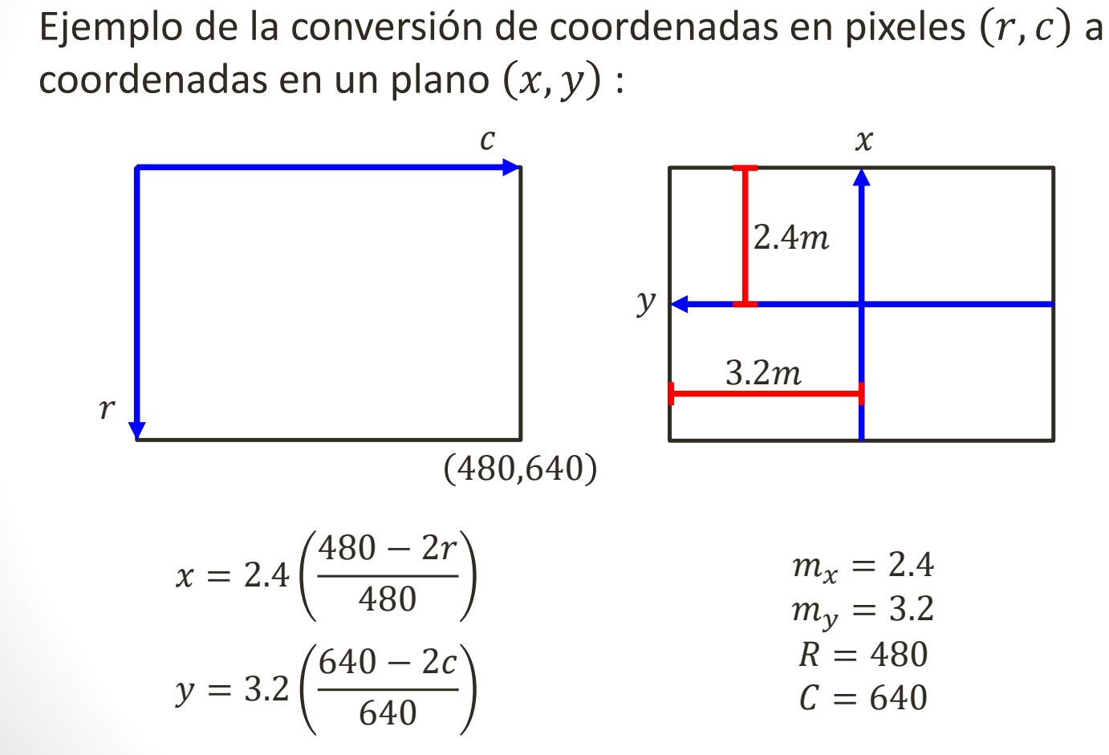
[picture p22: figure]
coordenadas en un plano x, y :

Ejemplo de la conversión de coordenadas en pixeles r, c a

15

## Planificación de trayectoria

Finalmente, el esquema recomendado para la planificación de trayectorias con datos obtenidos desde una cámara RGB es:

16

Imagen RGB

Escalamiento | Dilatación

Creación de
mapa

Generación de
trayectoria

Seguimiento de
trayectoria

Conversión trayectoria
al plano

## Planificación de trayectoria (continuación)

Ejemplos:

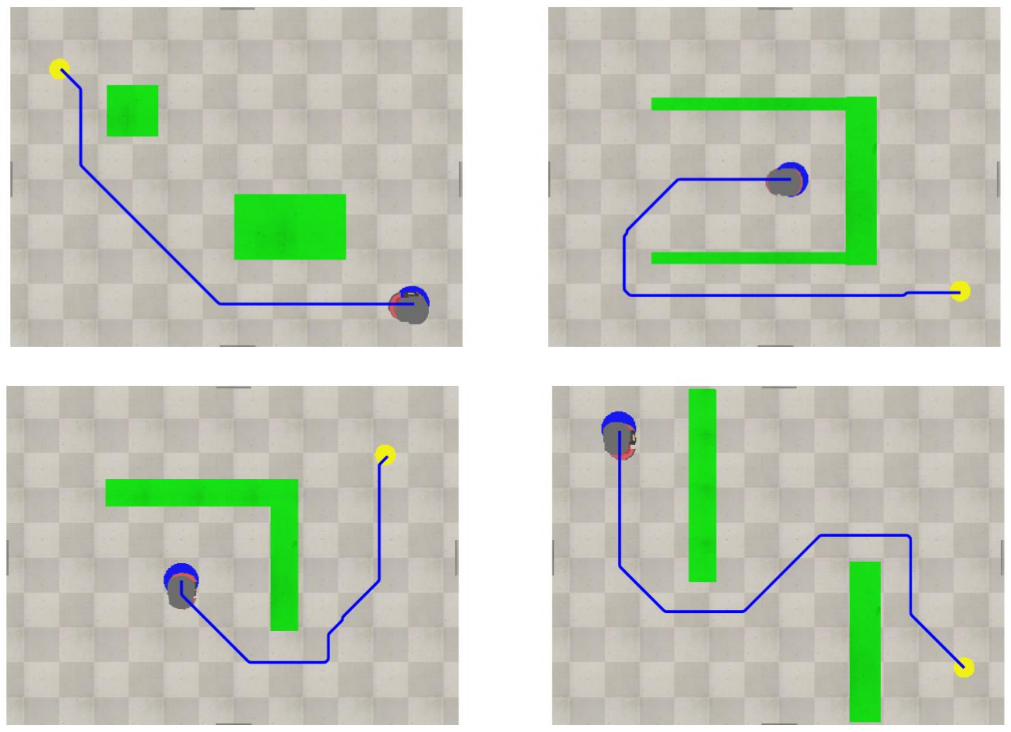
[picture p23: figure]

17

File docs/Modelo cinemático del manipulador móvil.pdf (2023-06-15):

# Modelo cinemático del manipulador móvil

Dr. José de Jesús Hernández Barragán josed.hernandezb@academicos.udg.mx

1

# Introducción

Los robots manipuladores móviles están compuestos por una plataforma móvil y uno o más manipuladores adheridos a la plataforma.

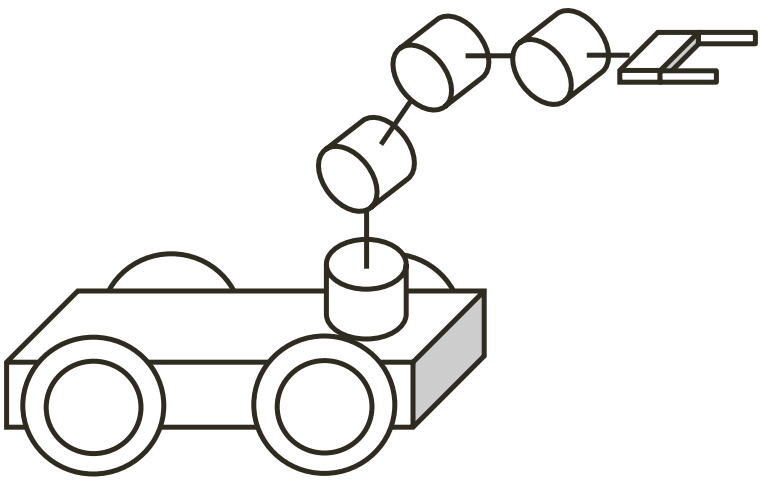
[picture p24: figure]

La cinemática de un manipulador móvil combina la cinemática de la plataforma móvil y del manipulador.

2

# Introducción (continuación)

Existen diversas combinaciones de plataformas móviles y manipuladores. Por ejemplo:

3


Ejemplo 1, imagen recuperada de: robotnik.eu/es/productos/manipuladores-moviles/manipuladores-xl-gen/ Ejemplo 2, imagen recuperada de: pinterest.com.mx/pin/373306256598726427/
Ejemplo 3, imagen recuperada de: robotmilitar.org
Ejemplo 1 | Ejemplo 2 | Ejemplo 3

# Cinemática directa

wTe =; wTp; bTe

Consideremos el siguiente manipulador móvil:

• “w” es el eje coordenado
del origen
• “p” es el eje coordenado
adherido a la plataforma
• “b” es el eje coordenado
base del manipulador
• “e” es el eje coordenado
del actuador final

La cinemática directa para el actuador final del manipulador
móvil se puede calcular como:

# Cinemática directa (continuación)

plataforma móvil. Definimos; pbase =; wTp =; cos θb; − sin θb; sin θb

Para calcular wTp debemos tener en cuenta la pose de la

Podemos construir la transformación homogénea wTp como

5

# Cinemática directa (continuación)

Para calcular p
Tb debemos consultar la hoja de datos del fabricante o medir físicamente la posición del manipulador con respecto a la base móvil.


6

# Cinemática directa (continuación)

Para calcular la matriz homogénea bTe debemos resolver la cinemática directa del manipulador.

La cinemática directa la podemos calcular utilizando

- La convención de Denavit-Hartenberg (DH)
- Método geométrico

Por conveniencia se propone utilizar la convención DH.

7

# Cinemática directa (continuación)

0Tn qarm =; de las articulaciones del manipulador; qarm =; donde; si i es rotacional; si i es prismática

Podemos calcular la cinemática directa de un manipulador como

donde 0Tn representa la pose del actuador final y n es el total de DOF.

El vector de coordenadas generalizadas qarm contiene la configuración

# Cinemática directa (continuación)

cos θi; − sin θi cos αi; sin θi; cos θi cos αi; sin θi sin αi; ai cos θi; − cos θi sin αi; ai sin θi; sin αi; cos αi; , translaciones; 0Tn qarm .

La matriz homogénea i−1Ti

se calcula de la siguiente manera

donde se considera una rotación θi en el eje zi
el eje xi

, di en los ejes xi y zi

respectivamente, y una rotación αi en

Finalmente, tenemos que bTe =

# Cinemática inversa

métodos: • Cinemática diferencial • Método geométrico; definida como

La cinemática inversa se puede resolver con alguno de los siguientes

Podemos calcular la cinemática inversa para un manipulador móvil con base en su cinemática diferencial. La cinemática diferencial esta

Además, despejando el valor de qሶ tenemos

donde xሶ representa el vector de velocidades de variables de actuación. 10

# Cinemática inversa (continuación)

Si definimos la velocidad del actuador final como xሶ = e,

- xd es la posición deseada para el actuador final del
- xi es la posición actual para el actuador final
- qሶ y q es la velocidad y la posición de las articulaciones del

# Cinemática inversa (continuación)

12

Es conveniente definir una matriz definida positiva K (usualmente, diagonal) para ponderar las velocidades del actuador final, es decir

qሶ = J qi

−1 Ke

Si la matriz K cumple con ser definida positiva, entonces el error e tiende a cero, es decir Ke = 0. Por lo tanto, se dice que el sistema es asintóticamente estable.

Recordemos que:
Una matriz M ∈ ℝ

n×n
con valores reales es definida positiva si
- x

TMx > 0 ∀ x ∈ ℝ

n ȁ x ≠ 0
- Los valores propios λi de M son positivos
Asintóticamente estable – Las condiciones iniciales convergen al punto de equilibrio

# Cinemática inversa (continuación)

diagrama de bloques.; Debemos tener en cuenta que si J q; −1 no es cuadrada,; Penrose.

El algoritmo de cinemática inversa se muestra en el siguiente

entonces es conveniente utilizar la Pseudo inversa de Moore-
13

# Cinemática inversa (continuación)

Resumen Algoritmo Cinemática Inversa; Paso 1: Definir lo siguiente xd, q0,t,K; (cinemática directa); Paso 3: Calcular el error e = xd − xi; cercano a cero, es decir Ke → 0

Paso 2: Calcular la posición actual T qi

Paso 4: Resolver cinemática diferencial qሶ = J qi

Paso 5: Resolver paso de integración qi+1 = qi + qሶt

Paso 6: Repetir pasos 2-5 hasta que el error e tienda a un valor 14

# Aplicabilidad

antropomórfico.; wTp =; cos θb; − sin θb; sin θb; pbase =

Ejemplo 1: Considere un manipulador compuesto por una plataforma omnidireccional y un manipulador de 3 DOF

Definimos la siguiente transformación para la plataforma móvil

15

# Aplicabilidad (continuación)

Se propone utilizar la siguiente transformación para definir la posición del manipulador con respecto a la base móvil.

p
Tb =

1 0 0 0.25
0 1 0 0
0 0 1 0.25
0 0 0 1

Esta matriz contiene los ajustes necesarios para encontrar la transformación homogénea entre los marcos de referencia ‘p’ y ‘b’.
16

# Aplicabilidad (continuación)

Respecto al manipulador antropomórfico, tenemos lo siguiente

Eslabón; qarm =

17

# Aplicabilidad (continuación)

cos θ1; sin θ1; 0 − cos θ1; cos θ2; −sin θ2; 0 0.30 cos θ2; sin θ2; 0 0.30 sin θ2; cos θ3; −sin θ3; 0 0.25 cos θ3; sin θ3; 0 0.25 sin θ3

Por lo tanto, podemos construir las siguientes matrices homogéneas

# Aplicabilidad (continuación)

Dado que bTe entonces tenemos que; bTe =; wTe =; wTp pbase; bTe qarm; donde; pbase =; qarm =

representa la cinemática directa del manipulador,

La cinemática directa para el manipulador móvil se calcula como

19

# Aplicabilidad (continuación)

cinemática diferencial definida como; donde; xሶb yሶb θሶ b θሶ 1 θሶ 2 θሶ 3

Para el calculo de la cinemática inversa, partimos de la

20

# Aplicabilidad (continuación)

xሶb yሶb θሶ b θሶ 1 θሶ 2 θሶ 3; donde las funciones tx, ty y tz; las podemos obtener a partir de; wTe =

La matriz Jacobiana la podemos calcular como

21

# Aplicabilidad (continuación)

teniendo en cuenta lo siguiente; xሶb yሶb θሶ b θሶ 1 θሶ 2 θሶ 3; † pseudo inversa

Podemos calcular la cinemática inversa del manipulador móvil

22

# Aplicabilidad (continuación)

función de un error; xሶb yሶb θሶ b θሶ 1 θሶ 2 θሶ 3; actual del actuador final.

Expresamos la cinemática inversa del manipulador móvil en

donde xd, yd, zd es una referencia y x, y, z es la posición

# Aplicabilidad (continuación)

Agregamos a la cinemática inversa del manipulador móvil una matriz para la controlabilidad del sistema

donde k1, k2 y k3 son ganancias positivas. | 24

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
k1 | 0 | 0
0 | k2 | 0
0 | 0 | k3

xd − x
yd − y
zd − z

# Aplicabilidad (continuación)

o también,; cos θ; −sin θ; sin θ; xሶb; yሶb θሶ b; 2 sin α; − 2 cos α; 2 cos α

Finalmente, utilizamos el modelo del omnidireccional para mapear las
velocidades xሶb, yሶb, θሶ
de la plataforma.

b a cada una de las velocidades de las ruedas

Modelo omnidireccional de 4 ruedas:

# Aplicabilidad (continuación)

26

Modelo omnidireccional de 3 ruedas:; − sin θ; cos θ; − sin θ +; cos θ +; xሶb yሶb θሶ b

# Aplicabilidad (continuación)

antropomórfico.; la plataforma omnidireccional.; wTe =; wTp pbase; bTe qarm

Ejemplo 2: Considere un manipulador compuesto por una plataforma modelo monociclo y un manipulador de 3 DOF

En este caso, la cinemática directa se define igual que el caso de

Sin embargo, es necesario considerar las restricciones del modelo monociclo para limitar el movimiento de la plataforma.
27

# Aplicabilidad (continuación)

manera vectorial, tenemos; xሶbsin θ − yሶbcos θ = 0; sin θ; − cos θ; xሶb yሶb θሶ b

Dada la restricción no-holonómica del monociclo y expresada de

28

# Aplicabilidad (continuación)

Utilizando le modelo Jacobiano e incluyendo la restricción no-holonómica en la matriz Jacobiana, expresamos la cinemática

29

Aplicabilidad (continuación); xሶb yሶb θሶ b θሶ 1 θሶ 2 θሶ 3; ∂tz ∂xb sin θ; ∂tz ∂yb − cos θ

Finalmente, agregamos a la cinemática inversa del manipulador móvil una matriz para la controlabilidad del sistema

donde k1, k2 y k3 son ganancias positivas. | 30

# Aplicabilidad (continuación)

velocidades xሶb, yሶb, θሶ plataforma.; Modelo monociclo; cos θ; sin θ; xሶb yሶb θሶ b

Finalmente, utilizamos el modelo del monociclo para mapear las b a cada una de las velocidades v, w de la

31

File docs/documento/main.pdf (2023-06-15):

## Universidad de Guadalajara


## CUCEI

## Proyecto Modular

## Equipo Amistad

## Briseño García Jorge Beto

## Briseño García Edna Elizabeth

## Muñoz Nuñez Ian Emmanuel

INCE - INRO | CUCEI

### 1. Cinemática directa

### 1.1. Modelado del youBot Arm


Figura 1: youBot Arm

### 1.2. Fórmulas y propiedades

n−1Tn =

Cθn | −Sθn Cαn | Sθn Sαn | anCθn
Sθn | Cθn Cαn | −Cθn Sαn | anSθn
0 | Sαn | Cαn | dn
0 | 0 | 0 | 1

sin(α ± β) = sin(α) cos(β) ± cos(α) sin(β) cos(α ± β) = cos(α) cos(β) ∓ sin(α) sin(β)

### 1.3. Tabla de parámetros Denavit-Hartenberg

| α | a | d | θ
1 | π 2 | 0 | d1 | 0
2 | 0 | a2 | 0 | 0
3 | 0 | a3 | 0 | 0
4 | 0 | a4 | 0 | 0

Tabla 1: Tabla de parámetros Denavit-Hartenberg

### 1.4. Matrices de transformación

0T1 =

C1 0 | S1 | 0
S1 | 0 −C1 0
0 0 | 1 | 0
0 0 | 0 | 1

1T2 =

C2 −S2 0 a2C2

S2 | C2 | 0 a2S2
0 | 0 | 1 | 0
0 | 0 | 0 | 1

2T3 =

C3 −S3 0 a3C3

S3 | C3 | 0 a3S3
0 | 0 | 1 | 0
0 | 0 | 0 | 1

3T4 =

C4 −S4 0 a4C4

S4 | C4 | 0 a4S4
0 | 0 | 1 | 0
0 | 0 | 0 | 1

0T4 =

0T1

1T2

2T3

3T4

### 1.5. Cinemática directa del youBot Arm

0T2 =

C1C2 −C1S2 | S1 | a2C1C2
S1C2 | −S1S2 | −C1 | a2S1C2
S2 | C2 | 0 | a2S2 + d1
0 | 0 | 0 | 1

0T3 =

C1C2C3 − C1S2S3 | −C1C2S3 − C1S2C3 | S1 | a3C1C2C3 − a3C1S2S3 + a2C1C2
S1C2C3 − S1S2S3 | −S1C2S3 − S1S2C3 | −C1 | a3S1C2C3 − a3S1S2S3 + a2S1C2
S2C3 + C2S3 | −S2S3 + C2C3 | 0 | a3S2C3 + a3C2S3 + a2S2 + d1
0 | 0 | 0 | 1

0T3 =

C1C23 −C1S23 | S1 | a3C1C23 + a2C1C2
S1C23 | −S1S23 | −C1 | a3S1C23 + a2S1C2
S23 | C23 | 0 | a3S23 + a2S2 + d1
0 | 0 | 0 | 1

0T4 =

C1C23C4 − C1S23S4 | −C1C23S4 − C1S23C4 | S1 | a4C1C23C4 − a4C1S23S4 + a3C1C23 + a2C1C2
S1C23C4 − S1S23S4 | −S1C23S4 − S1S23C4 | −C1 | a4S1C23C4 − a4S1S23S4 + a3S1C23 + a2S1C2
S23C4 + C23S4 | −S23S4 + C23C4 | 0 | a4S23C4 + a4C23S4 + a3S23 + a2S2 + d1
0 | 0 | 0 | 1

0T4 =

C1C234 −C1S234 | S1 | a4C1C234 + a3C1C23 + a2C1C2
S1C234 | −S1S234 | −C1 | a4S1C234 + a3S1C23 + a2C1C2
S234 | C234 | 0 | a4S234 + a3S23 + a2S2 + d1
0 | 0 | 0 | 1

0T4 =

C1C234 −C1S234 | S1 | C1(a4C234 + a3C23 + a2C2)
S1C234 | −S1S234 | −C1 | S1(a4C234 + a3C23 + a2C2)
S234 | C234 | 0 | a4S234 + a3S23 + a2S2 + d1
0 | 0 | 0 | 1

### 1.6. Cinemática directa de la plataforma omnidireccional

x˙
y˙
˙θ
- =

cos(θ) − sin(θ) 0
sin(θ) cos(θ) 0
0 | 0 | 1

1 −1 −(L + l)
1 | 1 | (L + l)
1 | 1 | −(L + l)
1 −1 | (L + l)

†

v1
v2
v3
v4

### 1.7. Cinemática inversa de la plataforma omnidireccional

v1
v2
v3
v4

=

1 −1 −(L + l)
1 | 1 | (L + l)
1 | 1 | −(L + l)
1 −1 | (L + l)

cos(θ) − sin(θ) 0
sin(θ) cos(θ) 0
0 | 0 | 1

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
2 sin(α) −

√
2 cos(α) −(L + l)
√
2 cos(α)

√
2 sin(α) (L + l)
√
2 cos(α)

√
2 sin(α) −(L + l)
√
2 sin(α) −

√
2 cos(α) (L + l)

x˙
y˙
˙θ

α = θ +

π
4

### 1.8. Cinemática directa desde el origen hasta el efector final

- w: Eje coordenado del origen.
- p: Eje coordenado adherido a la plataforma.
- b: Eje coordenado de la base del manipulador.
- e: Eje coordenado del actuador final.

wTe =

wTp

pTb

bTe

wTp =

cos(θp) − sin(θp) 0 xp
sin(θp) cos(θp) 0 yp
0 | 0 | 1 0
0 | 0 | 0 1

Con xp y yp como la posición del robot y θp como la orientación.

pTb =; bTe =; wTb =; cos(θp) − sin(θp) 0 0.170 cos(θp) + xp sin(θp) cos(θp) 0 0.170 sin(θp) + yp

x = CθC1(a4C234 + a3C23 + a2C2) − SθS1(a4C234 + a3C23 + a2C2) + 0.170Cθ + xp y = SθC1(a4C234 + a3C23 + a2C2) + CθS1(a4C234 + a3C23 + a2C2) + 0.170Sθ + yp z = a4S234 + a3S23 + a2S2 + d1 + 0.060

wTe =

CθC1C234 − SθS1C234 | −CθC1S234 + SθS1S234 | CθS1 + SθC1 | x
SθC1C234 + CθS1C234 | −SθC1S234 − CθS1S234 | SθS1 − CθC1 | y
S234 | C234 | 0 | z
0 | 0 | 0 | 1

wTe =

Cθ1C234 | −Cθ1S234 | Sθ1 | Cθ1(a4C234 + a3C23 + a2C2) + 0.170Cθ + xp
Sθ1C234 | −Sθ1S234 | −Cθ1 | Sθ1(a4C234 + a3C23 + a2C2) + 0.170Sθ + yp
S234 | C234 | 0 | a4S234 + a3S23 + a2S2 + d1 + 0.060
0 | 0 | 0 | 1

### 1.9. Cinemática diferencial

Jv(q) =

∂p1(q)
∂q1

∂p1(q)
∂q2

∂p1(q)
∂qn
∂p2(q)
∂q1

∂p2(q)
∂q2

∂p2(q)
∂qn
∂pm(1)
∂q1

∂pm(q)
∂q2

∂pm(q)
∂qn

tx = Cθ1(a4C234 + a3C23 + a2C2) + 0.170Cθ + xp ty = Sθ1(a4C234 + a3C23 + a2C2) + 0.170Sθ + yp tz = a4S234 + a3S23 + a2S2 + d1 + 0.060

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
= −Sθ1(a4C234 + a3C23 + a2C2) − 0.170Sθ

∂tx
∂θ1

= −Sθ1(a4C234 + a3C23 + a2C2)

∂tx
∂θ2

= −Cθ1(a4S234 + a3S23 + a2S2)

∂tx
∂θ3

= −Cθ1(a4S234 + a3S23)

∂tx
∂θ4

= −a4Cθ1S234

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
= Cθ1(a4C234 + a3C23 + a2C2) + 0.170Cθ

∂ty
∂θ1

= Cθ1(a4C234 + a3C23 + a2C2)

∂ty
∂θ2

= −Sθ1(a4S234 + a3S23 + a2S2)

∂ty
∂θ3

= −Sθ1(a4S234 + a3S23)

∂ty
∂θ4

= −a4Sθ1S234

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
= a4C234 + a3C23 + a2C2

∂tz
∂θ3

= a4C234 + a3C23

∂tz
∂θ4

= a4C234

Jv =

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
### 2. Control

### 2.1. Cinemática diferencial

x˙ = J(q) ˙q

### 2.2. Cinemática diferencial inversa

q˙ = J(q)

−1x˙

x˙ = e

e = (xd − xi)

q˙ = J(q)

−1x˙ | → | q˙ = J(q)

−1
e | → | q˙ = J(q)

−1
(xd − xi)

q˙ = J(q)

−1
(ke)

Siendo k una matriz definida positiva.

### 2.3. Modelo de control del Kuka YouBot Arm

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
q˙ =

x˙p
y˙p
˙θp
˙θ1
˙θ2
˙θ3
˙θ4

x˙ =

x˙
y˙
z˙

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

### 2.6. Modelo omnidireccional

v1
v2
v3
v4

=

1 −1 −(L + l)
1 | 1 | (L + l)
1 | 1 | −(L + l)
1 −1 | (L + l)

cos(θ) − sin(θ) 0
sin(θ) cos(θ) 0
0 | 0 | 1

⊤

x˙ p
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
2 sin(α) −

√
2 cos(α) −(L + l)
√
2 cos(α)

√
2 sin(α) (L + l)
√
2 cos(α)

√
2 sin(α) −(L + l)
√
2 sin(α) −

√
2 cos(α) (L + l)

x˙ p
y˙p
˙θp
- , α = θ +

π
4
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

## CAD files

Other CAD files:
3d/adapter.blend
3d/base.blend

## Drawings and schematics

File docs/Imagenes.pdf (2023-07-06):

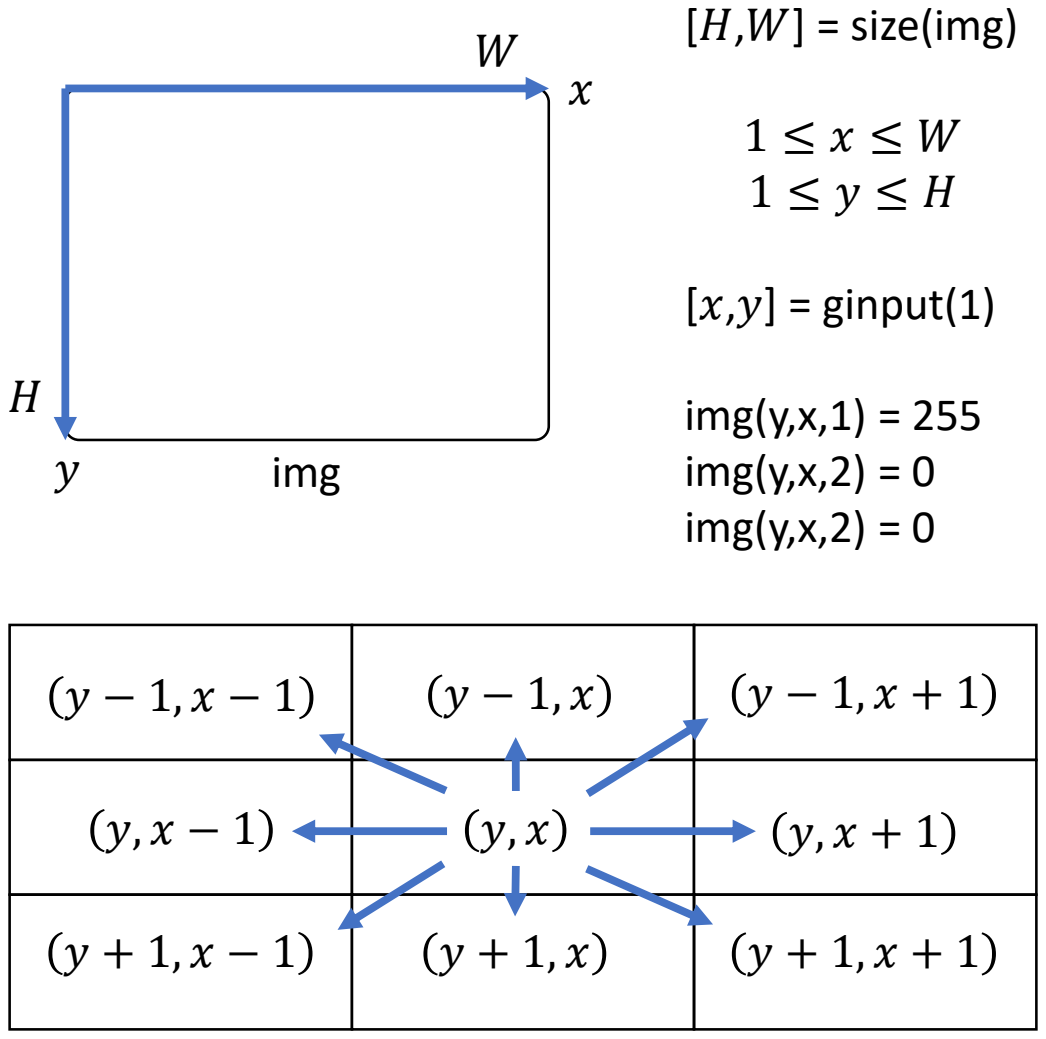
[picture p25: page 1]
[H,W] = size(img); [x,y] = ginput(1); img(y,x,1) = 255 img(y,x,2) = 0 img(y,x,2) = 0; img

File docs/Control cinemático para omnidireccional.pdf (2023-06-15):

# Control cinemático para omnidireccional

Dr. José de Jesús Hernández Barragán josed.hernandezb@academicos.udg.mx

1

# Preliminares

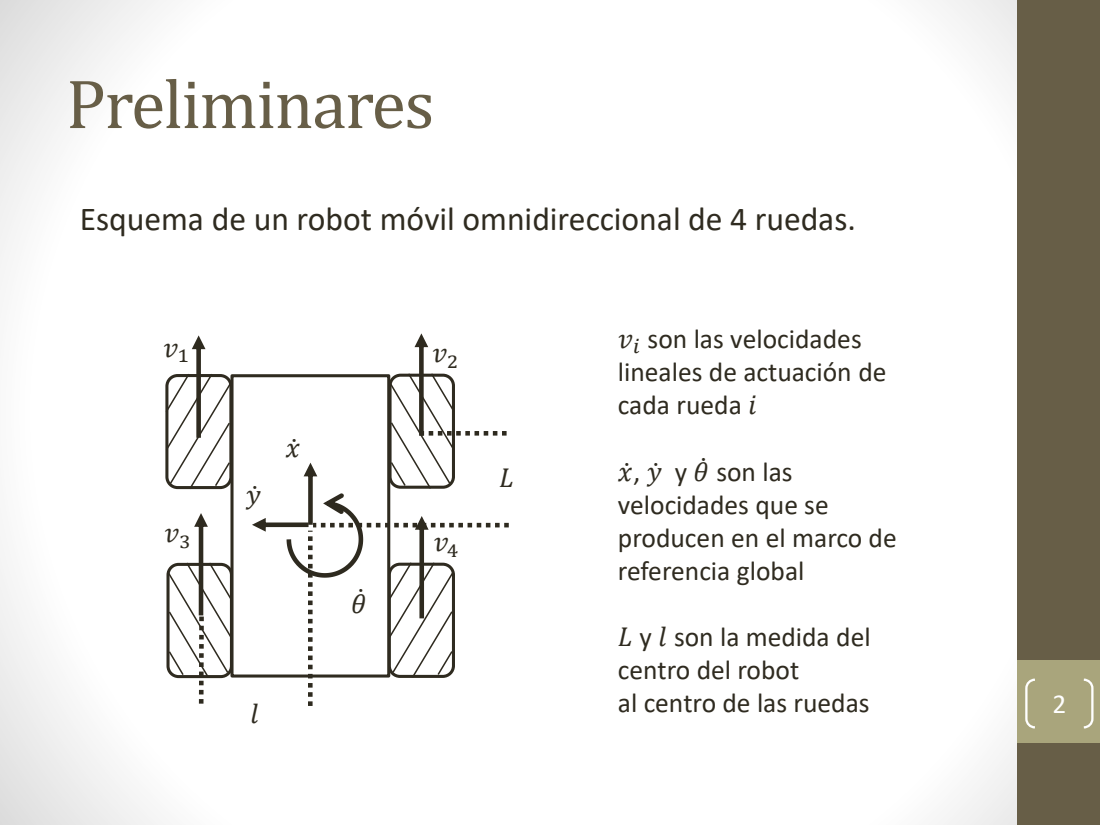
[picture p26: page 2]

Esquema de un robot móvil omnidireccional de 4 ruedas.

son las velocidades
lineales de actuación de
cada rueda i

xሶ, yሶ y θሶ son las
velocidades que se
producen en el marco de
referencia global

L y l son la medida del
centro del robot
al centro de las ruedas

# Preliminares (continuación)

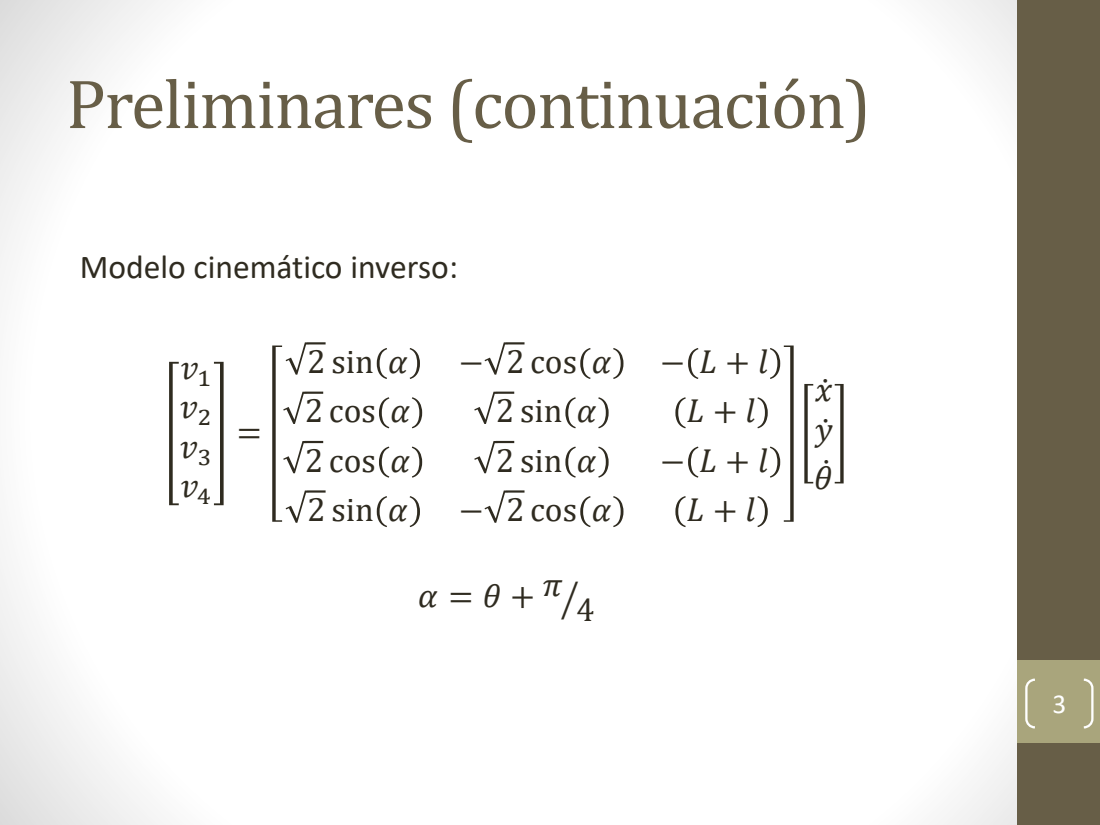
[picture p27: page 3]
2 sin α; − 2 cos α; 2 cos α

Modelo cinemático inverso:

## Control para omnidireccional

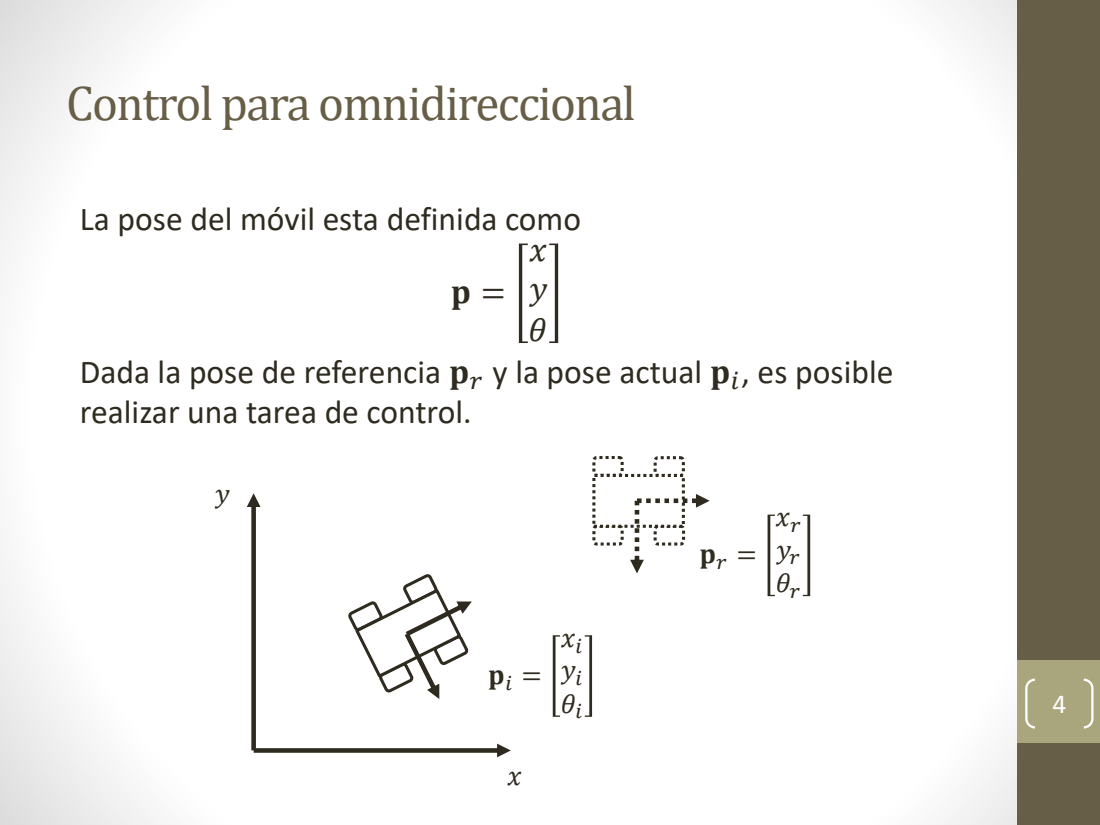
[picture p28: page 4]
, es posible

La pose del móvil esta definida como

Dada la pose de referencia pr y la pose actual pi
realizar una tarea de control.

## Control para omnidireccional (continuación)

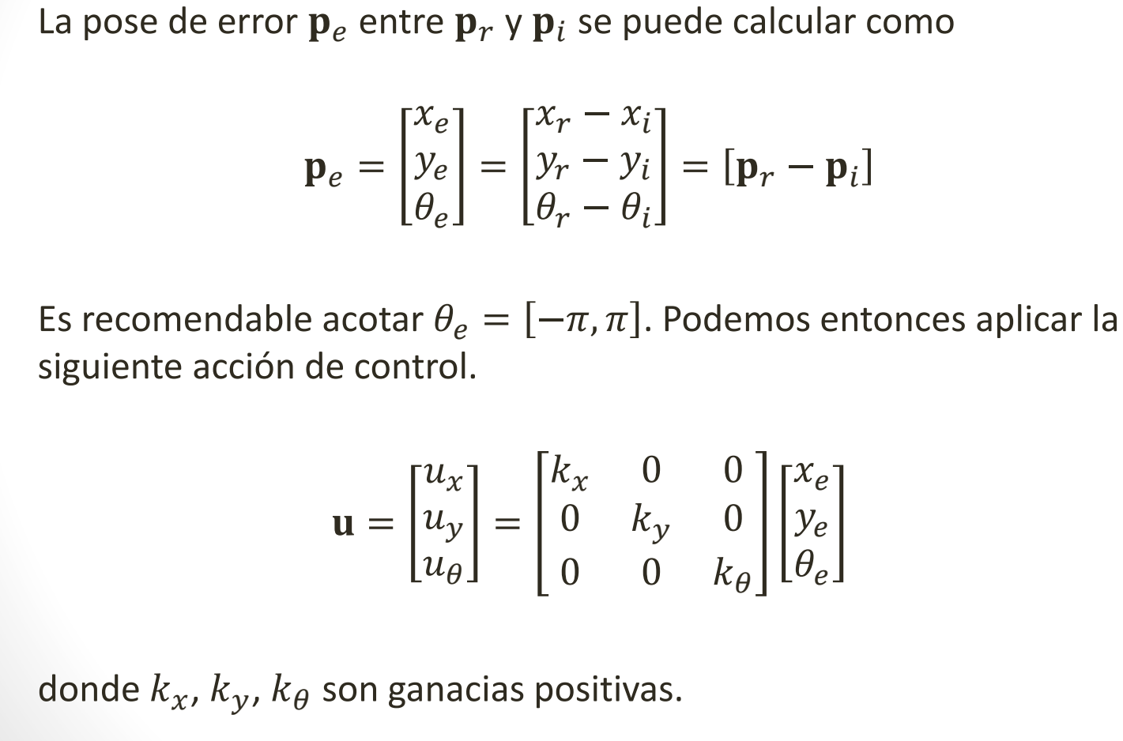
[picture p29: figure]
La pose de error pe entre pr y pi; se puede calcular como; Es recomendable acotar θe =; . Podemos entonces aplicar la; siguiente acción de control.

donde kx, ky, kθ son ganacias positivas.

5

## Control para omnidireccional (continuación)

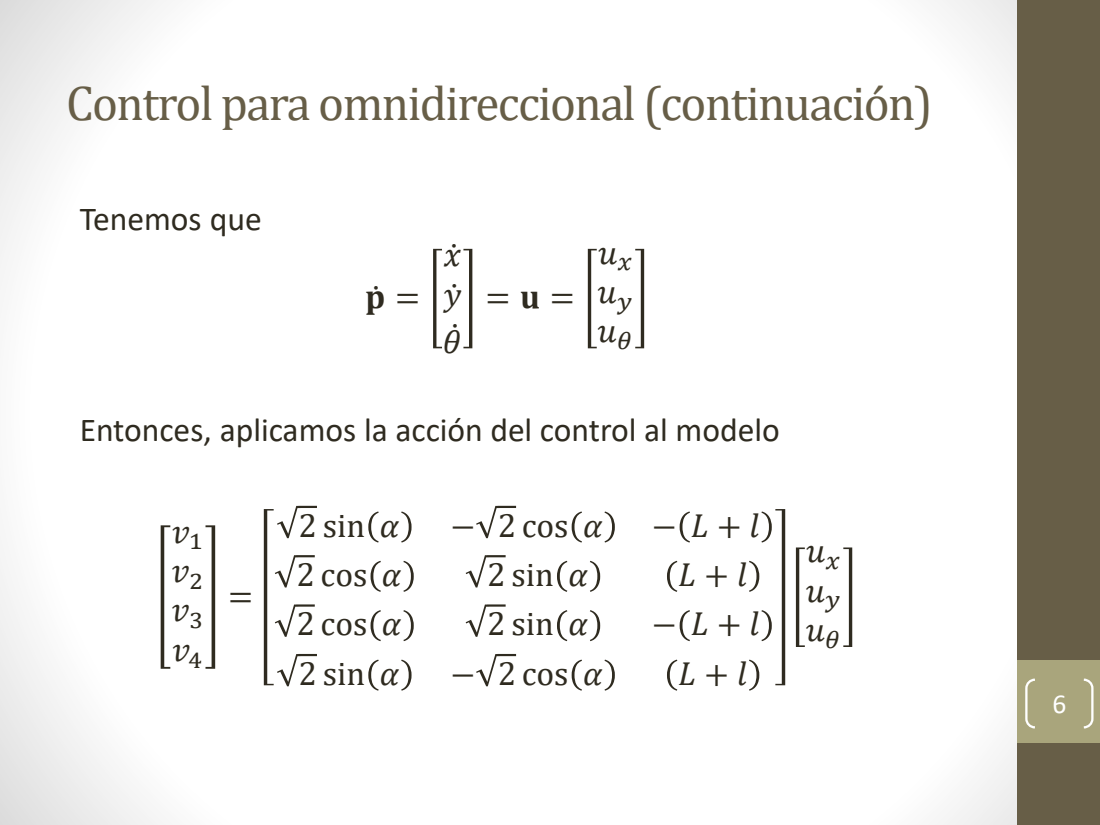
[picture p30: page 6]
Tenemos que; 2 sin α; − 2 cos α; 2 cos α

Entonces, aplicamos la acción del control al modelo

## Control para omnidireccional (continuación)

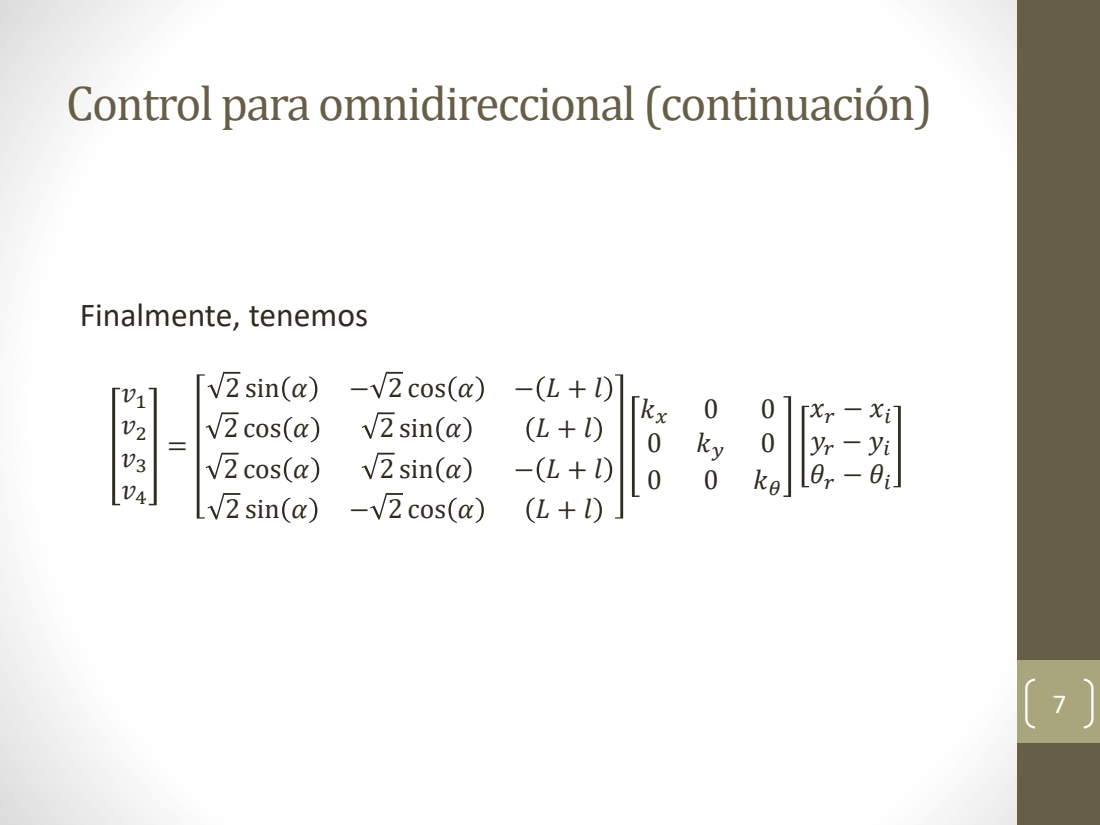
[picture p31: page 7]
Finalmente, tenemos; 2 sin α; − 2 cos α; 2 cos α

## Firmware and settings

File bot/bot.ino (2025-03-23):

#include <WiFi.h>

NetworkServer server(9999);

void blink(int,int);
void bot(NetworkClient);

int mf1 = 19;
int mf2 = 5;
int mf3 = 16;
int mb1 = 33;
int mb2 = 26;
int mb3 = 14;

const char* ssid = "esp32";
const char* password = "ciNNam0n2412";

IPAddress ip(192,168,1,32);
IPAddress gateway(192,168,1,1);
IPAddress subnet(255,255,255,0);

void setup()
{
  pinMode(2, OUTPUT);
  pinMode(mf1, OUTPUT);
  pinMode(mf2, OUTPUT);
  pinMode(mf3, OUTPUT);
  pinMode(mb1, OUTPUT);
  pinMode(mb2, OUTPUT);
  pinMode(mb3, OUTPUT);
  
  WiFi.mode(WIFI_STA);
  WiFi.config(ip, gateway, subnet);
  WiFi.begin(ssid, password);
  blink(2, 200);

  while(WiFi.status() != WL_CONNECTED)
  {
    delay(1000);
  }
  blink(3, 200);

  // Serial.begin(115200);
  // Serial.println("");
  // Serial.println("WiFi connected!!");
  // Serial.print("IP Address: ");
  // Serial.println(WiFi.localIP());

  server.begin();
}

void loop()
{
  NetworkClient client = server.accept();

  if(client)
  {
    // Serial.println("New Client Connected");
    bot(client);
  }
}

void bot(NetworkClient client)
{
  String velocidad1, velocidad2, velocidad3;
  int v1, v2, v3;
  
  while(client.connected())
  {
    if(client.available())
    {
      String msg = client.readStringUntil('\n');

      if(msg == "q") break;

      velocidad1 = msg.substring(0,4);
      velocidad2 = msg.substring(4,8);
      velocidad3 = msg.substring(8,12);

      v1 = velocidad1.toInt();
      v2 = velocidad2.toInt();
      v3 = velocidad3.toInt();

      if(v1 >= 0)
      {
        analogWrite(mb1, 0);
        analogWrite(mf1, v1);
      }
      else
      {
        analogWrite(mf1, 0);
        analogWrite(mb1, abs(v1));
      }

      if(v2 >= 0)
      {
        analogWrite(mb2, 0);
        analogWrite(mf2, v2);
      }
      else
      {
        analogWrite(mf2, 0);
        analogWrite(mb2, abs(v2));
      }

      if(v3 >= 0)
      {
        analogWrite(mb3, 0);
        analogWrite(mf3, v3);
      }
      else
      {
        analogWrite(mf3, 0);
        analogWrite(mb3, abs(v3));
      }
    }
  }
  client.stop();
  // Serial.println("Client Disconnected");

  analogWrite(mf1, 0);
  analogWrite(mf2, 0);
  analogWrite(mf3, 0);
  analogWrite(mb1, 0);
  analogWrite(mb2, 0);
  analogWrite(mb3, 0);
  
  blink(4, 500);
}

void blink(int iter, int t)
{
  for(int i = 0; i < iter; i++)
  {
    digitalWrite(2, HIGH);
    delay(t);
    digitalWrite(2, LOW);
    delay(t);
  }
}

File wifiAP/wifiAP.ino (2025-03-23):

#include <WiFi.h>
#include <WiFiAP.h>

#define LED 2

const char *ssid = "esp32";
const char *password = "ciNNam0n2412";

void blinking(int);

void setup()
{
  pinMode(LED, OUTPUT);

  blink(1);

  if(!WiFi.softAP(ssid, password))
  {
    log_e("Soft AP creation failed");
    while(1);
  }
  else
  {
    blink(2);
  }

  IPAddress myIP = WiFi.softAPIP();

  blink(3);
}

void loop()
{
}

void blink(int x)
{
  for(int i = 0; i < x; i++)
  {
    digitalWrite(LED, HIGH);
    delay(500);
    digitalWrite(LED, LOW);
    delay(500);
  }
}

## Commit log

2023-06-08 Seguimiento de trayectoria y control de brazo
    Seguimiento de trayectorias con el algoritmo 'WaveFront'
    usando la plataforma 'kuka' funcional y control del brazo
    'youBot' funcional.
2023-06-08 Workspace
    Espacio de trabajo del brazo 'youBot'.
2023-06-11 Control de manipulador
    Control del manipulador 'Kuka' con cinemática directa y
    diferencial en CoppeliaSim.
2023-06-15 Seguimiento de trayectorias y movimiento de objetos
    El robot sigue una trayectoria generada con el algoritmo
    'WaveFront' y al llegar al punto deseado manipula un
    objeto.
2023-07-06 Reconocimiento de arUco y pose
    Se reconoce un arUco con una cámara y se tiene su posición y
    orientación con la imagen.
2023-07-13 Graficas para la simulacion en coppeliaSim
    Se muestran gráficas al terminar la simulación de CoppeliaSim.
    Se usa una cámara externa apuntando al suelo para identificar
    la posición y pose de un arUco.
2023-07-31 Aplicacion de ESP32 y ESP32CAM
    Se hizo una conexión con la ESP32 para manejar el robot móvil
    y se probaron dos tipos de conexiones con la ESP32CAM para
    después localizar el robot con las cámaras.
2023-08-17 Posibles impresiones para el robot
    [52mm_Hub.stl, 52mm_Roller.stl]
2023-08-31 Cambio de modelo de robot a omnidireccional de 3 ruedas
    [52mm_Hub.stl, 52mm_Roller.stl]
2023-09-18 Actualizacion de codigo
    Actualización del código para la conexión con el esp32 a la
    computadora, ahora funciona con el modelo omnidireccional de
    3 ruedas. También se agregaron los datos de los participantes
    a los archivos.
2023-09-18 Punto de acceso
    Se realizó un código para crear un punto de acceso con una
    tarjeta esp32.
2023-09-18 Conexiones a red
    Se eliminaron el SSID y la contraseña de los archivos.
2023-09-23 README
    Se agregó un archivo 'readme.md' para tener un poco de
    documentación en el repositorio.
2023-10-17 Diseños 3D
    [base.blend, base.stl]
2023-10-29 Valores de PWM acotados y adaptador 3D agregado
    Se arreglaron los valores de PWM para que no pasen los valores
    de -1023 y 1023.
    Se actualizó el "readme.md" para Windows y Linux.
    Se agregó el modelo 3D del adaptador para ruedas y motores.
    [adapter.blend, adapter.stl]
2023-11-11 Medidas de motores, ruedas y camaras
2024-02-16 Adapter2.0: Nuevas medidas para adaptador
    [adapter.blend, adapter.stl, base.stl]
2024-02-22 Se agrego el modelo del perceptron multicapa
    [color.csv]
2025-03-23 bot and wifiAP added to repo
    - Test for connection between c server in esp32 for bot and
    python client successfully created
    - Access Point using C created successfully and working
